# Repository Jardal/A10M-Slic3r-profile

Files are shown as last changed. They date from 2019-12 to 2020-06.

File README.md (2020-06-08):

Slic3r A10M 3D printer profile
==============================

This is content of the folder and file structure from c:\Users\[yourname]\AppData\Roaming\Slic3r 

This profile is for genuine Slic3r.org slicer development version only, which you can download it here: https://dl.slic3r.org/dev/win/
Note that Slic3r need a lot of power to display itself, it will display slowly on machines with Atom or similar CPU.

**All settings are for UNTOUCHED printer as you got it from manufacturer.** 
Mine printer is with black SiC surface glass which is not need to use glue or something else. Sticking is not as good as with glue, but you easily take printed parts if hotbed is under 40°C.

All values are calculated to 340 extruder steps as in A10M factory firmware. If you have calibrated values or use 430 steps, set it to factory  values.

Printing speed is limited by volumetric speed to 10mm3/s. Physical limit of path extruder gear - hotend tip is about 13-15mm3/s. Because my extruder lever is broken after few weeks, I was print another and use bigger spring. Your gears should be clean, no splinters from filament, only small amount of white dust at both sides of saw wheel and filament way is mirrorish clean.
Do not use Speedy profiles if you are unsure about extruder driver status. Critical value of whole path is about 4-6mm3/s, so if you are under this limit, your prints are in higher quality. Values you can check in gcode output.

There is unique **implemented height-temperature response** which is good for free-air printing. I was discovered right values while printing of skewed vase mode complex models. But result is not as strong as high temperature prints.  

## Slicer picked options
 
#### Advanced
- Complete individual objects - for multiple printing objects - need 37mm space between, pay attention on XY axis when place objects with height over 27mm
- Infill/perimeter overlap - if your long bridge hairs are falling from edges, use bigger value
- XY Size  Compensation - compensation if you need to fit together (0.05mm mean 0.2mm difference in tolerance of joined diameters)

#### Extruders
options for dual material or color prints only
- Regions... overlap - give 0.05 to glue objects together or -0.25 or more to make separate objects

#### Extrusion width
Use values to fit your design or use "auto" value together with Fill gaps option checked. A10M AUTO have "auto" or "default" values enabled at all.
**External perimeters**
- upright and exact sizes are best with 0.42mm width
- universal or skewed design is best with 0.52mm but did not want exact holes (are smaller) and size in X-Y is slightly (way) bigger
- exact sizes or skewed vase mode 0.6mm (exact with with xy compensation -0.08mm)
- upright vase mode could be up to 0.8mm for better strongness  

#### Infill
- Infill patterns - Hilbert is for great adhesivity of bottom side. Other use as you want.
- FIll angle set to 90 if you want different bridge or top layer way.
- Fill density - use bigger values to make it strength, but 10% and 3 shells is enough
- FIll gaps - worse print quality, better strength, did not use it at very small or complex tiny detail objects
- Combine Infill - for speed-up prints, less strength if values >1
- Infill before perimeters - use it if you need as much exact size of diameters or when infill destroy perimeters (ABS); use low infill only (10%)
- Only infill where needed - unchecked is for strong prints, checked acts as internal support material - speed-up prints, less strength (about 20% less)
- Solid infill treshold - about 5-10 for strong vertical  sticks, 0 for selected % infill only.  
- Solid infill every - is for better strength, but not as much. Use about 10 if you have horizontal holes for big screws.

#### Layers
- Use adaptive slicing - for models with many skews, Quality 75% is good for many details, 35% is good few details
- layer height - 0.3mm is maximum, for some colours (silver) 0.28. Thinner layer does not as much nicer finish as you think, but 0.2 are much stronger than 0.3. More height, more External perimeter width.
- Avoid crossing - if on, then printing quality of small details is much worse, leave it off (maybe disappear in future - future is now)
- External perimeters First - if you want to have as much exact surfaces as possible. Disable it at very small pieces if you dont want to use brim.
- Only retract when... - disable it in rare case of simple objects or if you print infill only without perimeters (aka negative vase mode), enabled for spedd-up print
- Bottom/Top layers - these values are as minumum, did not use less. If you print with thin layers, increase both values. More layers = more strength
- Perimeters - 2 is too low (big impact to quality, about 20% less strength), 3 is nice. More perimeters = more strength about 2-3% only and worse quality of details, but holes with big screws you can tight more with 4-5 and 40% infill

#### Guide to change parameters by layer height
| Layer height   | 0.3 | 0.2 - 0.25 | 0.1 - 0.15| note |
| infill overlap | 25  | 15         |  0 | quality |
| perimeters     | 3   | 3          |2|  at least |
| ext perimeter width | 0.56 | 0.45 | 0.45 | best values |
| perimeter width     | 0.56 | 0.45 | 0.45 | ... |
| first layer width | 0.52   | 0.42 | 0.42 | ... |
| infill extr. width | 0.56  | 0.45 | 0.45 | ... |
| ext. perimeter speed | 30  | 30    | 25| hardness and quality |
| top solid infill speed | 30 | 30    | 20| by mean of quality |
| bottom solid layers| 3    | 3     | 4| at least |
| top solid layers|    3    | 4     | 6| strength |
| bridge flow ratio |  0.95 | 0.95  |0.8| quality |

#### Speed
- External - bigger speed = worse detail, worse strength
- First - if you print tiny objects, use lower value (10) for better adhesivity. At extra large objects it prevents corner warping.

## Complex objects guide
#### Print settings
- HQ/AUTO - select what is better for your model (see Preview)
- Speedy Gonzales is faster print
- Speedy McQueen is fastest print as possible, quality is not measure
- MULTI PLY 2,5mm is profile for thin multiple objects up to 2,5mm, printed in completation sequence, not at one. My A10M have vertical space between nozzle tip and PLA cooling fan mouth 2,5mm. Measure your printer first! Use with CARDS filament profile and HQ/AUTO printer.
#### Filaments
- Speed - for speed prints
- Dark/Light - about filament colour
- CARDS - for thin cards or very tiny or thin objects with small height - note that strongness is much worse. If you print a boomerang, use Speedy Gonzales Light + STRONG
- STRONG - for strong, lower complexity  objects; Set Infill/perimeter overlap to 60%, xy size -0.015, perimeters width 0.52 and 0.56, fill gaps on; How it is different from LightSpeedy: fan is off, fatter extrusion multiplier, limited volumetric speed.
#### Printer
- STRONG - for strong objects, it does not have height temperature profile as others do. Reccomended with LightSpeedy or STRONG filament settings, but quality is lower due high-temp artifacts while retraction
- HQ/Speed - correspond with Print settings

## Vase mode prints guide
#### Print settings
- vase HQ for highest quality of print
- vase Speedy Gonzales is fast print
- Vase Paper-thin - if you need paperweight vase mode figures
#### Filament
- vase HD - for high details prints
- vase BLACK - for asphaltic black colour only
- Light Speedy - for all other colours - if it does high-temp artifacts, use dDark Speedy or Dark only.
#### Printer
- Simple Vase for simple vase models without retractions
- Strong if object is not slashed
- HQ/Speedy if vase is relative complex object with needed retractions

## Dual colour print configuration
For bucket and switching filaments (no mixing at the moment)
- Print: HQ/Speed
- Filament: DUAL
- Printer: DUAL

## Tricks
- print models near back of build plate, it will save your cables
- try to print "body" of the vase model by setting perimeters to zero.
- objects could be printed as vase too if you need it for measuring if it will fit to. If object is multipart, export whole bed from Slic3r as STL and import this file instead
- Support is needed only in rare case, adaptive mode prints from about 10 deg withut it.
- Microsoft 3D Builder is not bad for editing models. But Tinkercad is better for exact construction work.
- Geeetech in download section have Color Mixer software, try it. It supplies mixer from control Panel, but way better.
- if you need dual coloured part, go to Settings button...
- Each gcode file from Slic3r contain at the end whole printing configuration which could be imported to Slic3r again
- Each gcode file contain at the begin all settings what you set it at the right panel for future reference (and you did not need to make printscreen with settings)
- Slic3r remember settings and you want to begin with defaults? Simply edit file slic3r.ini and delete row with last_output_path and whole sections Presets and Recent.
- Dual colour print should be used without filament cleaning, but remember that to change colour it need about 25mm in extruder (ie., 25-50 cm of transient colour to fully change colour). You slould set same value (2 for left extruder) to Infill and Perimeter extruder in Extruders section
- You can check gcode health with Pronterface http://kliment.kapsi.fi/printrun/ . just associate gcode files with Pronterface... See Internet Archive if link disappeared: https://web.archive.org/web/20191031020314/http://kliment.kapsi.fi/printrun/
- Strongest pieces you will get with layers 0.2 or 0.15mm, about 10% less with thinner print and about 50% less with 0.3mm
- Infill does not have such impact on strongness as you think. 3 perimeters and 10% infill are about 10% less than 100% infill

## Notes about material
**Profile is for ABS only**. Best colours for quality printings are white, yellow, green, light gray. Bad colors are silver, black. Use plastics without smell, they are way better than fume filaments.

Remember, that ABS is not able to print curves in free air as PLA wit appropriate cooling blower, bridges only.
 
## How to make good printer
### Tighten it all
Printers need to be tightened after shipping shocks. Use only manual screwdriver to tighten all screws and wheels except the wheels at the right side of X arm. Hotbed springs need to be slightly tightened too, so you could put Z-axis switch to 1-2mm lower position for greater stiffness. 
### Lubricate it all
Use gun oil to lubricate bearings and lithium vaseline to the Z-axis rod and gears in the extruder (except saw wheel of course).
### Do it at the first
- filament filter
- dual colour bucket
- extruder lever
- Cable pathway helper
- LED lightning in the top-dovn V-slot(2x 10cm LED 12V strip in series), powered from PSU, but you must know what you do, otherwise your printer will be burned. Possible version for "civilians": https://www.thingiverse.com/thing:4089189
- fan silencer (note that for 2019/10 version is needed only one for PSU)
- use plastic shopping bag as dust shield for top of printer with filament spools
- cover hotbed at least with sheet of paper if you leave your printer cold 

...Files, images or links will be added later, stay tuned. 
 
## Repair parts
- Extruder Lever for print in Repair parts folder (lever which I was edited but forged from where it is - if you are original author, leave a note here)
- Extruder Nozzle tip
- Fittings
- PTFE (teflon) tube
- V-slot wheels
- GT2 belt
- Thermistor in glass B3950 100k 1m
- 40W/24V heater element 30mm (or 20mm)
- 3010 24V fans
- 4010 24V blowing fan
- PLA fan duct for 4010 fan
- 4010 24V system unit fan

## Tuning parts
- Waste bucket for dual colour prints
- Bed heihgt wheels
- filament filter
- Thumb wheels for Titan extruder lever spring
- Cable pathway helper
- fan silencer for PSU - simply resize it to 168% in slicer and tight it with one screw only. It is about 12% oversized because it is exhaust side - https://www.thingiverse.com/thing:2988448 
  Of course you can try newer versions with phase invertors https://www.thingiverse.com/thing:2988448
- fan silencer for system unit (not for 2019/10+ model) with 8010 12V fan and mini DC/DC step-down module
- extruder support for tall prints 
- Back-up UPS 700VA or more (not each 500VA will work)
- 4020 24V blowing fan with PLA fan duct and extended drive capability to 0-255 PWH with arduino+NPN (DIY). Small flow is needed for ABS, high for PLA, but small flow 35% is too high for ABS with bigger fan. 

## Servicing Printer
- Clogged bowden - https://www.youtube.com/watch?v=uKxPIGal74E
- What you often need to do if you does not have filament filter - https://www.youtube.com/watch?v=hOKSaBrxTDs
- Attention! thermistors are connected from 5V to Ain instead of Ain to GND. Easy to burn out mainboard!

## Main differences A10M over generic CR10 printer
- modularized system unit - you can replace stepper driver
- you did not tunings - are already done

## Wizard
It is possible to make application which will create right configuration based on questions and answers. Or Machine learning/AI based analysis of object. You can do it.

## Missing options in Slic3r
with settings for A10M with black glass
- Printer/Extruder/Wipe + [x] do not wipe first layer  [] do not wipe top layer  [x] do not wipe short tracks below [3 mm]
- Print/Infill/Print gaps + [x] do not fill gaps on first layer  [x] do not fill gaps on top layer
- Print/Layers/External perimeters first + From layer [3] 

with settings for A10 with PEI sheet
- Printer/Extruder/Wipe + [x] do not wipe first layer  [x] do not wipe top layer  [x] do not wipe short tracks below [3 mm]
- Print/Infill/Print gaps + [x] do not fill gaps on first layer  [x] do not fill gaps on top layer
- Print/Layers/External perimeters first + From layer [2] 

...formated by using https://medium.com/swlh/how-to-make-the-perfect-readme-md-on-github-92ed5771c061

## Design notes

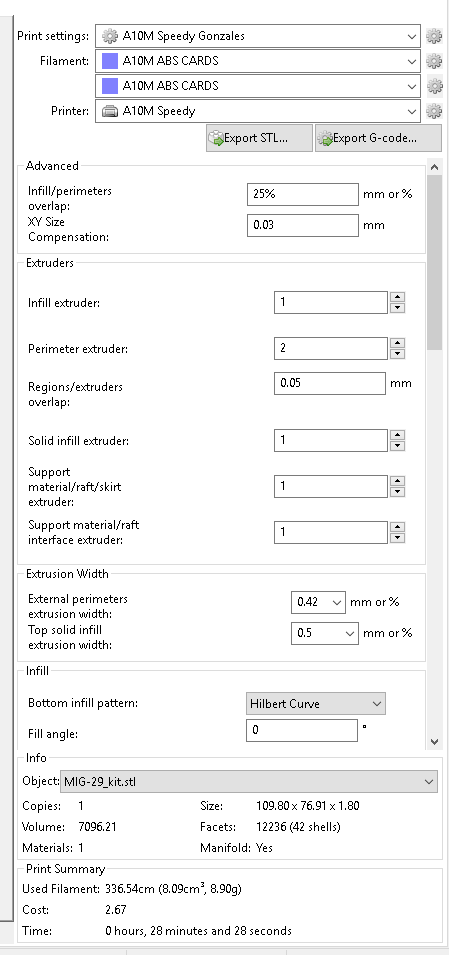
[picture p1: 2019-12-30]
ADDONS/Dual color examples/MIG-29_kit SG DUALxy+003.png

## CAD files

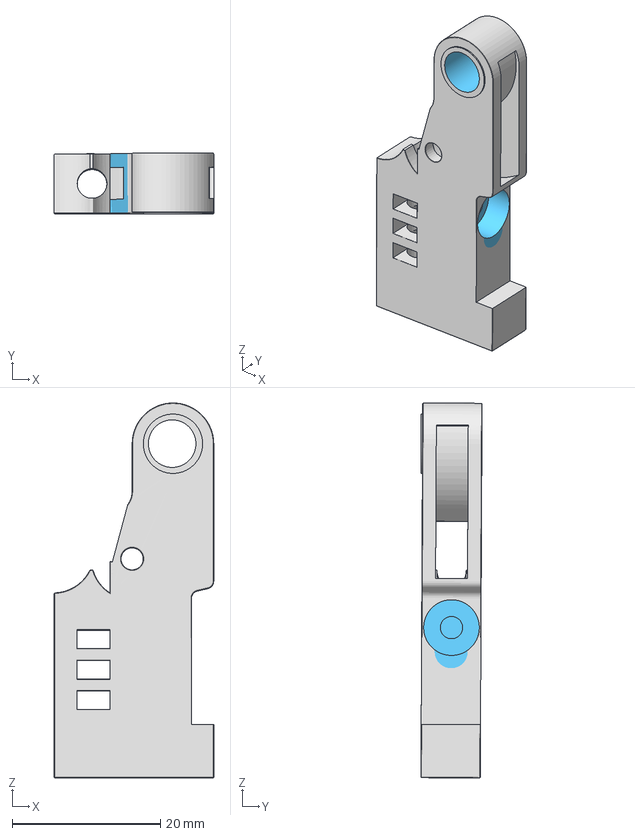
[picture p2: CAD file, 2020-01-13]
ADDONS/Repair parts/Idler_Arm A10M for 20mm springs - cutted idler.3mf
21.5 x 8.25 x 50.5 mm

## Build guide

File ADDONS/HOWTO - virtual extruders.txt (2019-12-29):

This is a quick tutorial on how to setup and use Virtual Extruders on printers with mixing hotends such as the Geeetech A10M and A20M.  

I used Simplify3D for this tutorial because the interface showed well on camera, but because this process is mostly in the startup script, ANY slicer that supports multi-extruders will work.

The startup Gcode for this process is:
M163 S0 P1.00 ; Set Left to 100%
M163 S1 P0.00 ; Set Right to 0%
M164 S0 ; Save Mix

M163 S0 P0.00 ; Set Left to 0%
M163 S1 P1.00 ; Set Right to 100%
M164 S1 ; Save Mix

M163 S0 P0.50 ; Set Left to 50%
M163 S1 P0.50 ; Set Right to 50%
M164 S2 ; Save Mix

Etc….

Remember on the M164 command, this is the number of the extruder/Toolhead  you will assign, minus 1. i.e. S0 = Extruder 1, S1 = Extruder2,  S2 = Extruder 3 (first virtual extruder), etc.

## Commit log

2020-01-05 extended options, new profile
    New profile for thin multiple objects up to 2,5mm, printed in completation sequence, not at one. My A10M have vertical space between nozzle tip and PLA cooling fan mouth 2,5mm. Measure your printer f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
2020-01-13 Default values, simplified interface
    Often changed default values are now default, picked options slightly simplified, added more.
    Repair section added.
    [Idler_Arm A10M for 20mm springs - cutted idler.3mf]
2020-01-14 VASE mode multiple copies allowed; printer STRONG temp correction
2020-02-23 Strong filament profile added
2020-03-21 Create A10M Old Shatterhand.ini
    profile for strong prints
2020-04-14 Dynamic filament feed added
    Low layers are too fat. One simple solution is to modify amount of filament to few following layers
